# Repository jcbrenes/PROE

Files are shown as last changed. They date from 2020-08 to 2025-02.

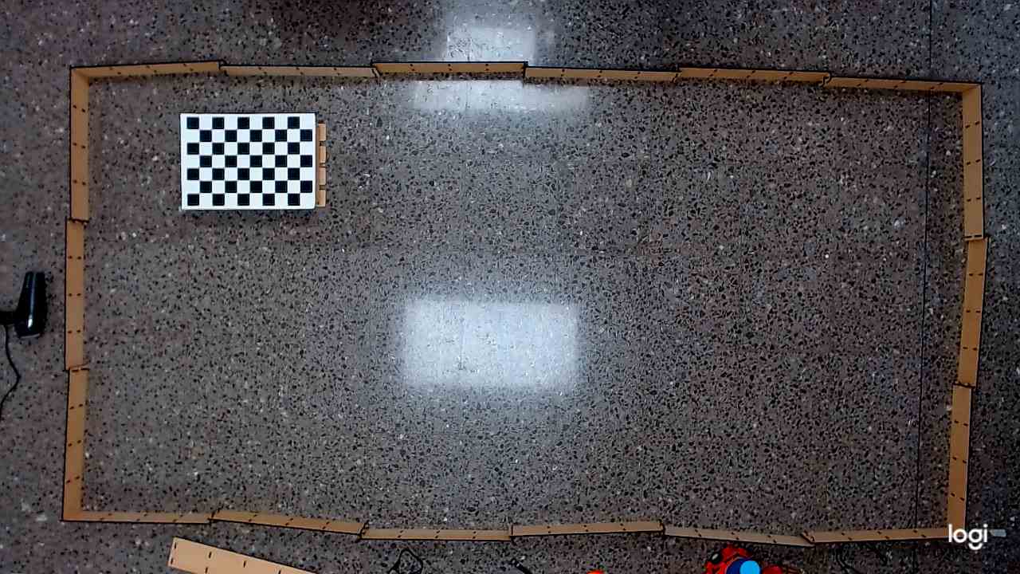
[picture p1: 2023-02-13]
Herramientas/Cámara/VALIDACION_PYTHON/Calibración Python/Imagenes_Calibracion_Nueva_Sala/2022-10-19_15-29-37.jpg

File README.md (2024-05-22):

# Repositorio de software para el proyecto PROE
PROYECTO PROE: Implementación de un prototipo de enjambre de robots para la digitalización de escenarios estáticos y planificación de rutas óptimas.

Proyecto de investigación del Instituto Tecnológico de Costa Rica, dirigido por la Escuela de Matemática y con participación de la Escuela de Ingeniería Mecatrónica.

Este proyecto pretende diseñar un sistema multirobot físico para la exploración de escenarios estáticos desconocidos, con el fin de determinar rutas óptimas. Dicha implementación significa una traducción y adaptación de los algoritmos computacionales de exploración investigados en el proyecto “PROE: Simulación computacional para la planificación de rutas óptimas de acceso y/o evacuación por medio de un enjambre centralizado en escenarios estáticos, utilizando técnicas de mapeo, procesamiento de datos y optimización multiobjetivo” (PROE E1F1 ); además de implementar técnicas de recolección, transferencia y procesamiento de datos para mapear la zona y así poder determinar rutas de acceso y/o evacuación seguras.

Los códigos computacionales, archivos CAD, diagramas eléctricos, esquemas de ensamblaje, lista de materiales y demás documentación acá presente representan el esfuerzo llevado acabo en este proyecto.

Directorio de archivos:
- Arquitectura_PROE-> archivo PDF de la arquitectura del sistema electrónico
- Corte_Chasis_PROE -> archivo PDF para corte láser del chasís 
- Corte_Obstaculos_PROE -> archivo PDF para corte láser de los obstáculos del escenario 
- PCB_Conexiones_PROE-> archivo PDF con la conexiones del PCB
- BOM_PROE -> archivo con la lista de materiales para el proyecto PROE
- EstandarCodigo -> Lineamientos para escritura de código en el proyecto
- Readme 
- LICENSE

Directorio de carpetas:
- PROE_LOCOM -> Proyecto en Arduino IDE (placa Feather M0) para Locomoción y Comunicación
- PROE_DETOB -> Proyecto en Arduino IDE (placa Bluepill STM32) para Detección de Obstáculos
- PROE_COMBASE -> Proyecto en Arduino IDE (placa Feather M0) dispositivo usado como base para la comunicación
- Chasis: archivos CAD para corte láser del chasís
- Obstáculos: archivos CAD para corte láser de los obstáculos
- PCB: archivos CAD para diseño del PCB y archivos Gerber para manufactura del PCB
- Herramientas: archivos para calibración y validación
	- Vision_Validacion -> herramienta de Matlab para validar giros y desplazamientos de un robot
	- Vision_Patron -> archivo PDF del patrón que debe aparecer en las imágenes para calibrar
	- Vision_Guia -> archivo PDF de la figura que debe ubicarse en cada robot para seguimiento
	- Calibracion_Motores -> archivo para correr en feather y calibrar los motores
	- Calibración_Magnetómetro -> archivo para correr en feather y calibrar el magnetómetro

Investigadores: 
- Cindy Calderón Arce (ccalderon@itcr.ac.cr). Escuela de Matemática, Tecnológico de Costa Rica. Coordinadora Proyecto  
- Rebeca Solís Ortega (rsolis@itcr.ac.cr). Escuela de Matemática, Tecnológico de Costa Rica. 
- Juan Carlos Brenes-Torres (juanbrenes@tec.ac.cr). Escuela de Mecatrónica, Tecnológico de Costa Rica. Encargado del desarrollo de software y hardware para los robots AttaBots del proyecto PROE.

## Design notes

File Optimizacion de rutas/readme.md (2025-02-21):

En la carpeta Processing se encuentran los documentos mayormente relacionados al procesamiento de datos.

Dentro se encuentra la carpeta mapeo en donde están todos los archivos. Esto es porque processing tiene la similitud con Arduino de que el archivo mapeo.pde debe estar dentro de una carpeta llamada igual, o sea, mapeo.

En este directorio deben estar las carpetas de videos "1_robot", "2_robot" y "3_robot" que corresponden a procesamiento offline. También está el programa de processing, "mapeo.pde", el cual funciona de la siguiente forma:
1. Se ejecuta el script clickeando en la flecha en la parte superior del programa.
2. Se da click al círculo grande de cada robot para comenzar a seguir ese color.
En ese entonces se crea una carpeta llamada "prueba" (o algo así) dentro de la cual se generan las carpetas "divided_color_matrix" y "reduced_color_matrix", dentro de las cuales, asimismo, se generan las matrices correspondientes, cada 10 segundos. Dentro de esta carpeta se debe poner el video grabado de dicha prueba y nombrar la carpeta de forma adecuada al final de la prueba.

Además, está el programa de R, "Graficas", que se encarga de realizar los gráficos de análisis estadístico con base en los archivos "Principal" y "Resumen". Estos dos archivos son generados por un programa de Python de otra carpeta que se explica a continuación.

----------------------------------------------------------

En la carpeta Python se encuentra el programa para realizar el procesamiento de las matrices generadas por Processing. Si se desea realizar el procesamiento en tiempo real, se debe abrir el programa "main ONLINE.py" después de abrir "mapeo.pde". Este programa genera en la carpeta "prueba" anteriormente mencionada las carpetas "A", "D", "Dict", "Graph", "P" y el archivo "path_objective_Cob", los cuales se van actualizando en tiempo real según la velocidad de procesamiento de la computadora.
OJO esto quiere decir que processing y python son ASINCRÓNICOS.

El programa "análisis_datos.py" accede a las carpetas "1_robot", "2_robot" y "3_robot" mencionadas anteriormente y, asimismo, accede a cada carpeta "5-1", "5-2", ..., "15-13" y toma las matrices de cada prueba para realizar dos informes estadísticos, uno llamado "Principal", el cual contiene las estadísticas descriptivas en cuartiles, y "Resumen", el cual contiene un resumen o promedio de "Principal".

En la carpeta "Procesamiento offline" se encuentran distintos programas según la necesidad, pero en general, el único necesario es "main OFFLINE.py", el cual genera lo mismo que el ONLINE. Los demás se utilizaron una vez, no deberían ser necesarios, pero igual se dejaron por si acaso.

Los demás archivos son dependencias para el main, los cuales no se deben tocar y no es importante explicarlos.

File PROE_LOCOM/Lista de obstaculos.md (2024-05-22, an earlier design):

# Lista de mensajes

Distribución de los mensajes:
- Los mensajes se componen de 7 valores separados por ";" y el orden de lectura es:
	- ID: número de identificación del robot
	- Coordenada X
	- Coordenada Y
	- Orientación
	- Tipo de mensaje
	- Distancia a obstaculo: para sensor sharp
	- Ángulo de obstaculo: para sensor sharp

El tipo de mensaje indica a que se refiere el resto de la información en el mensaje.

Lista de tipos de mensajes que se van a recibir en la base:
- 0: Identifica posición sin obstaculo
- 1: Sharp, da medida de distancia y ángulo
- 2: IR frontal
- 3: IR derecho
- 4: IR izquierdo
- 5: Temperatura
- 6: Batería baja 
- 15: El Atta completó la función avanzarCoordenada y deja de avanzar
- 20: Medición de distancia inicial para coordinación de coordenadas
- 40: Falla de magnetómetro
- 41: Falla de MPU

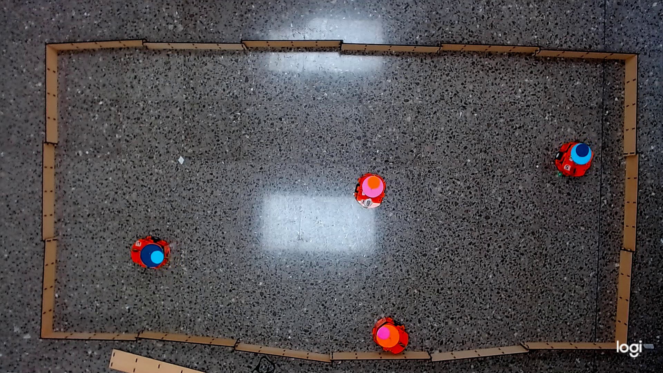
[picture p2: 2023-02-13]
Herramientas/Cámara/VALIDACION_PYTHON/Validación Python/ImagenesRbk/frame34.jpg

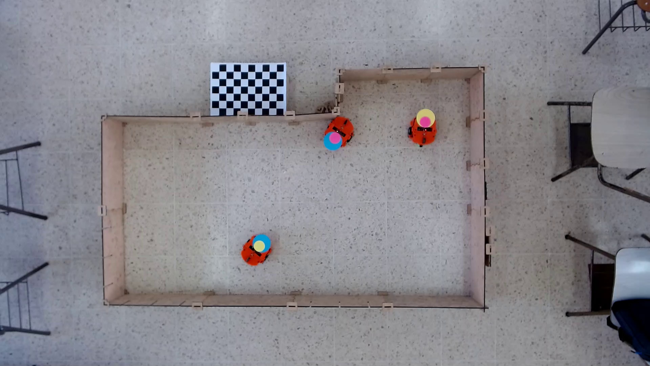
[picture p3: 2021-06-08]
Herramientas/Cámara/VALIDACION_ANTERIOR/Segmentación por color/ImagenesRbk/frame14.jpg

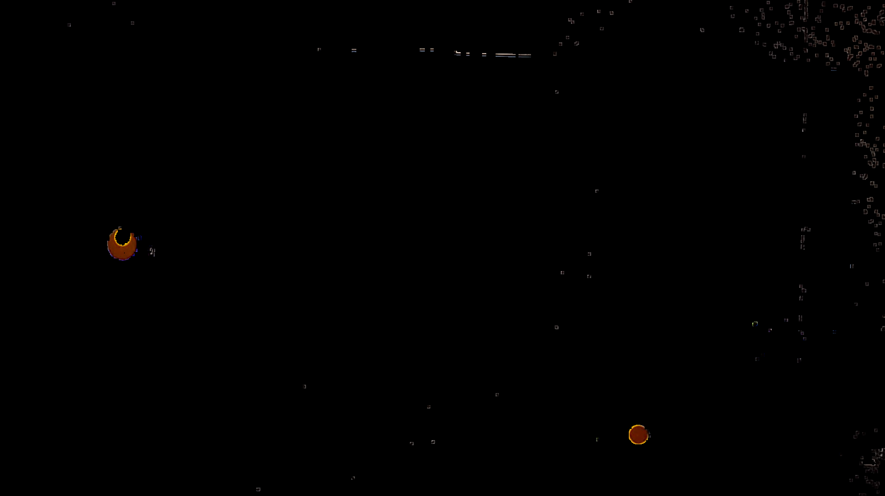
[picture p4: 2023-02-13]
Herramientas/Cámara/VALIDACION_PYTHON/Validación Python/filtrado_azul3.png

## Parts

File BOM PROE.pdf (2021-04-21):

Materiales para la construcción de 1 agente robot de PROE

Cantidad | Nombre | Número parte Link | Costo CR /u
1 | Batería Lipo 2Ah | ADA-328 | https://www.crcibernetica.com/lithium-ion-polymer-battery-3-7v-2500mah/ | $14,95
1 | Boost | ADA-1903 | https://www.crcibernetica.com/powerboost-500-basic-5v-usb-boost-500ma-from-1-8v/ | $10,95
1 | Puente H (módulo) | TB6612FNG | https://www.crcibernetica.com/generic-motor-driver-1a-dual-tb6612fng/ | $4,95
2 | Motores DC encoder | ROB-CB0N20 https://www.crcibernetica.com/n20-gearmotor-with-encoder-and-wheel/ | $14,95
2 | Soporte motores | ROB-CB02443 https://www.crcibernetica.com/micro-gearmotor-support-bracket/ | $0,75
1 | Ball caster | ROB-CB1818 https://www.crcibernetica.com/3pi-n20-ball-caster/ | $2,75
1 | uC Feather M0 RFM69 | ADA-3176 | https://www.crcibernetica.com/adafruit-feather-m0-rfm69-packet-radio-868-or-915-mhz/ | $24,95
1 | Magnetómetro | IM130918001 https://www.crcibernetica.com/hmc5883l-triple-axis-compass-magnetometer-sensor-module/ | $9,95
1 | uC Blue Pill | DEV-CB02143 https://www.crcibernetica.com/stm32f103c8t6-arm-stm32-blue-pill-microcontroller-board/ | $4,95
1 | Servomotor | MG90S | https://www.crcibernetica.com/mg90s-micro-servo-with-metal-gears/ | $6,95
1 | Sensor IR adelante | SEN-CB0006 | https://www.crcibernetica.com/infrared-obstacle-avoidance-module/ | $2,95
2 | Sensor IR abajo | SEN-CB0005 | https://www.crcibernetica.com/track-sensor-module/ | $1,95
1 | Sensor Temperatura | SEN-10988 | https://www.crcibernetica.com/tmp36-temperature-sensor/ | $1,95
1 | Sensor sharp | IM130619002 https://www.crcibernetica.com/sharp-gp2y0a21yk-distance-measuring-sensor/ | $16,95
1 | Pines | PRT-00116 | https://www.crcibernetica.com/break-away-headers-straight/ | $1,95
1 | Interruptor general | COM-CB0372 https://www.crcibernetica.com/slide-switch/ | $1,25
1 | Interruptor pequeño | COM-09609 | https://www.crcibernetica.com/spdt-slide-switch/ | $0,95
1 | LED azul | COM-11372 | https://www.crcibernetica.com/led-basic-blue-5mm/ | $0,15
1 | LED rojo | COM-09594 | https://www.crcibernetica.com/led-basic-yellow-5mm/ | $0,15
1 | LED amarillo | COM-09590 | https://www.crcibernetica.com/led-basic-red-5mm/ | $0,15
1 | IMU | MPU-6050 | https://www.crcibernetica.com/mpu-6050-triple-axis-accelerometer-and-gyroscope-module/ | $6,95
1 | Memoria eeprom | AT24C16 | https://www.microjpm.com/products/at24c16-two-wire-serial-eeprom/ | $1,40
3 | Capacitores poliester 100nF | | https://www.microjpm.com/products/a100if-100v-capacitor-poliester-metalizado/ | $0,40
3 | Header hembra 40 pines 1 fila | | https://www.microjpm.com/products/conector-hembra-de-40pins-2-54mm-una-fila-/ | $0,80
2 | Conector de motor hembra | JST-ZH | https://www.ebay.com/itm/JST-ZH-1-5mm-Pitch-4-Pin-Right-Angle-Male-PCB-Connector-Shrouded-Header-x-100/172462947325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 -
1 | Conector de la bateria | JST-PH | https://www.ebay.com/itm/JST-PH-2-0mm-Pitch-2-Pin-Male-Right-Angle-Connector-Shrouded-Header-Socket-x-100/181461829632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 -
1 | Base DIP 8 pines | https://www.ebay.com/itm/100PCS-DIP8-Integrated-Circuit-8-Pin-IC-Sockets-Adaptor-Solder-Type-New/173695893286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 -
Otros | (Estos componentes se comparten entre varios robots)
Cantidad | Nombre | Modelo | Link | Costo CR
Programador Blue Pill | DEV-CB0468 | https://www.crcibernetica.com/st-link-v2-mini-programmer-color-may-vary/ | $5,95
Cable USB | CAB-10215 | https://www.crcibernetica.com/usb-microb-cable-80-cm/ | $4,95
Caja Espaciadores y tornillos | TOL-CB0513 | https://www.crcibernetica.com/m3-nylon-screw-black-hex-screw-nut-nylon-pcb-standoff-assortment-kit-250pcs/ $15,95
| Caja Resistencias | COM-10969 | https://www.crcibernetica.com/resistor-kit-1-4w-500-total/ | $11,95

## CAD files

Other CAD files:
Chasis/Chasís PROE.dwg
Herramientas/Cámara/VALIDACION_ANTERIOR/Códigos QR/ExportadorCodigosTamañoReal.dwg
Obstaculos/Obstaculos_PROE.dxf
Obstaculos/Obstaculos_PROE.dwg

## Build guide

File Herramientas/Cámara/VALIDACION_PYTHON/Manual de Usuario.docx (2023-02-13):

PROYECTO PROE

Manual de uso del Sistema de Visión (última actualización: 05/02/2023)

CONSIDERACIONES GENERALES

Para ejecutar los códigos se debe tener un ambiente programación como Jupyter Notebooks o Google Colab. Alternativamente, se pueden descargar todas las librerías requeridas y utilizar Python de forma local. Además, se debe contar con el software Logitech Capture para utilizar la webcam.

CALIBRACIÓN

1. Abrir el repositorio de PROE y buscar en la sección Herramientas/Cámara/VALIDACION_PYTHON/Calibracion Python.
2. Se debe disponer de al menos 10 imágenes de calibración utilizando el patrón correspondiente y colocándolo en diferentes posiciones. Las mismas deben ser tomadas con la webcam en la posición definitiva que se vaya a usar. Se adjuntan 4 imágenes a modo de ejemplo:

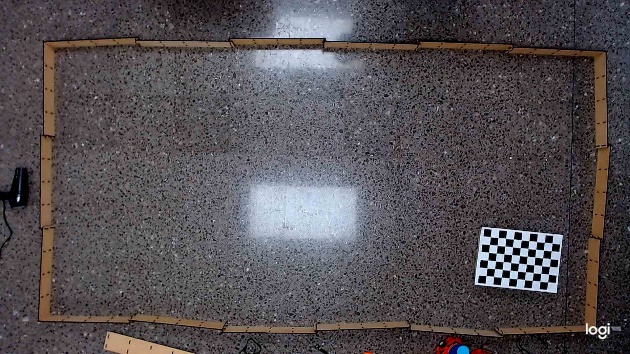
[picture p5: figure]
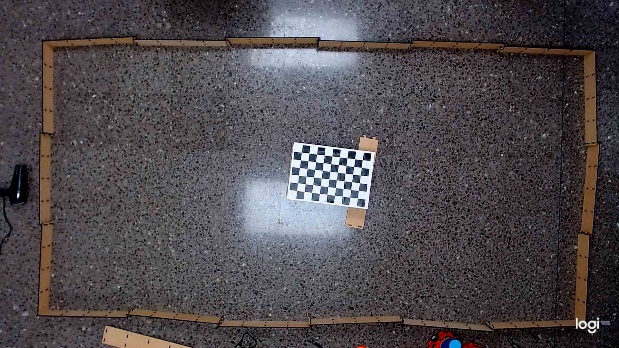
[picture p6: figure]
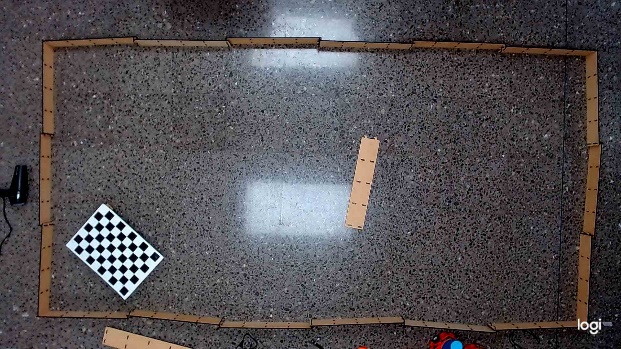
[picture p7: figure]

3. Agregar las imágenes de calibración al folder llamado “Imagenes_Calibracion_Nueva_Sala”.
4. Ejecutar el código llamado “Calibracion_Camara”
5. Se van a generar 2 archivos .txt en el folder, estos corresponden a las matrices de calibración necesarias.
6. Copiar ambos .txt y pegarlos dentro del folder Herramientas/Cámara/VALIDACION_PYTHON/ Validación Python.
7. Al finalizar la calibración, se debe ajustar el ratio de mm/pixeles dentro del código de Validacion. Esto se puede realizar con una de las imágenes de calibración tomadas en el punto 2. Se debe abrir la imagen en Paint, en el mismo se pueden visualizar los pixeles en forma de coordenadas (x,y) en la parte inferior, tal como se muestra en la imagen. Calcular la longitud del lado de un cuadrado del patrón (en pixeles) utilizando la fórmula para la distancia entre 2 puntos. Se sabe de antemano que el lado mide 40 mm.

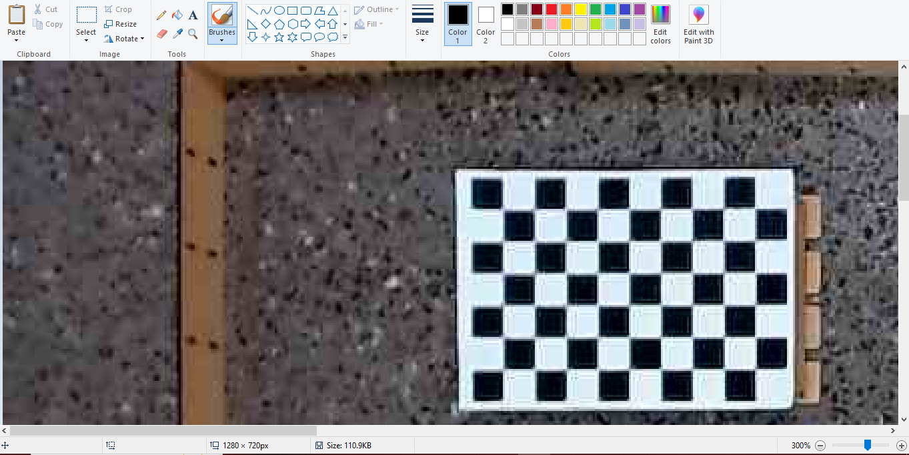
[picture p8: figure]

ratio [mm/pixeles]= (40 mm)/(Longitud del lado en pixeles)

8. Por último, actualizar valor en el código para la variable mmPixel, en ambas líneas. Tal y como se muestra a continuación.

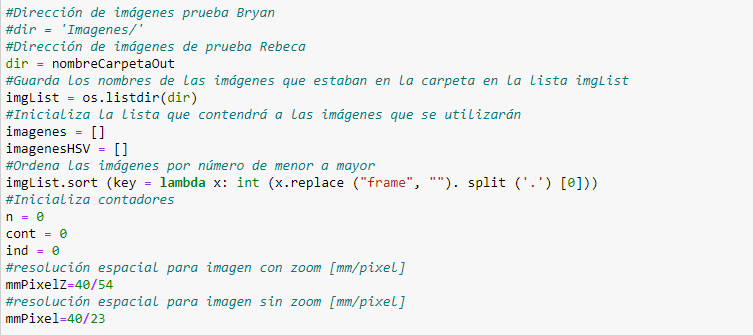
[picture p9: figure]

9. El sistema de visión está listo para ser usado. Se debe agregar un video a la carpeta Herramientas/Cámara/VALIDACION_PYTHON/Validación Python. El nombre se debe actualizar en la variable “nombreVideoIn”. Tener en cuenta las líneas señaladas en azul, dado que cada vez que se ejecuta un nuevo video el código lo descompone en imágenes y las guarda en la carpeta “ImagenesRbk”. Se deben descomentar esta líneas únicamente cuando se cambie de video y adicional a esto, se deben eliminar todas las imágenes de la carpeta “ImagenesRbk” antes de ejecutar el código con un nuevo video.

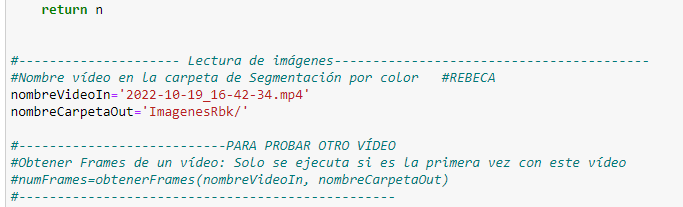
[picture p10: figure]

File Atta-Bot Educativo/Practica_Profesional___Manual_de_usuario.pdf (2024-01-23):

# Instituto Tecnológico de Costa Rica

## Escuela de Computación Ingeniería en Computación Practica profesional

Manual de usuario

## Simplificación de los Atta-Bots para un entorno educativo

## Estudiante:

2018189196 - Isaac David Ortega Arguedas

Fecha de entrega: 7 de Junio, 2023

## I semestre 2023

## Índice

1. Introducción | 2
2. Instalación | 2
3. Ejecución de la aplicación | 4
4. Utilización del programa | 4
5. Desinstalar la aplicación | 14
6. Conclusión | 15

1

## 1. Introducción

El presente documento es el manual de usuario del programa que será entregado por Isaac David Ortega Arguedas, como proyecto de la Practica Profesional para el primer semestre del 2023, a los miembros de investigación PROE, esto es para que tengan material de referencia en caso de tener alguna duda sobre el programa. Este manual va a cubre todos los pasos necesarios para el correcto uso de la aplicación incluyendo el proceso de instalación.

## 2. Instalación

Para instalar la aplicación solo se requiere ejecutar el instalador (ver Figura 1).

Figura 1: Instalador de Atta-Bots-Kids

Una vez ejecutemos el instalador se nos abrirá una ventana (ver Figura 2) en la cual se nos indica que indicara los pasos necesarios para instalar la aplicación. Para proseguir con la instalación pulsamos el botón ”Next”.

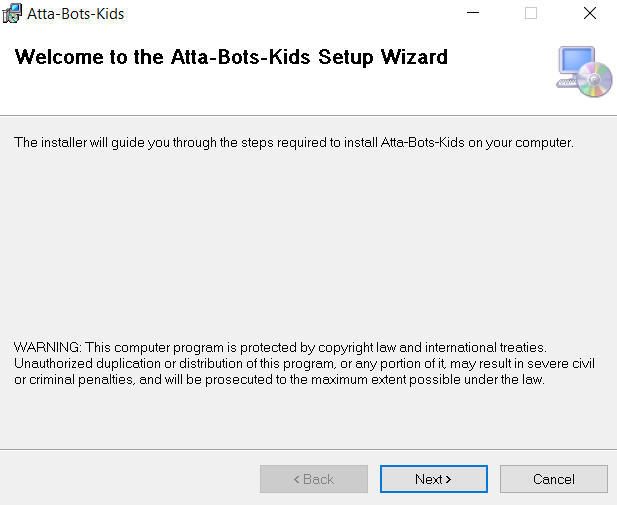
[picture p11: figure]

Figura 2: Confirmar que se quiere instalar la aplicación

En el segundo paso es para indicar donde deseamos instalar la aplicación, así como indicar si deseamos que la aplicación se instale para todos los usuarios de la computadora o solo para el usuario en el que nos encontramos actualmente (ver Figura 3). Ya se cuenta con una dirección por defecto, pero es si se desea cambiar dicha dirección es posible pulsando el botón ”Browse...”. Una vez hayamos escogido la dirección deseada, así como a quienes deseamos instalar la aplicación pulsamos el botón ”Next”.

2

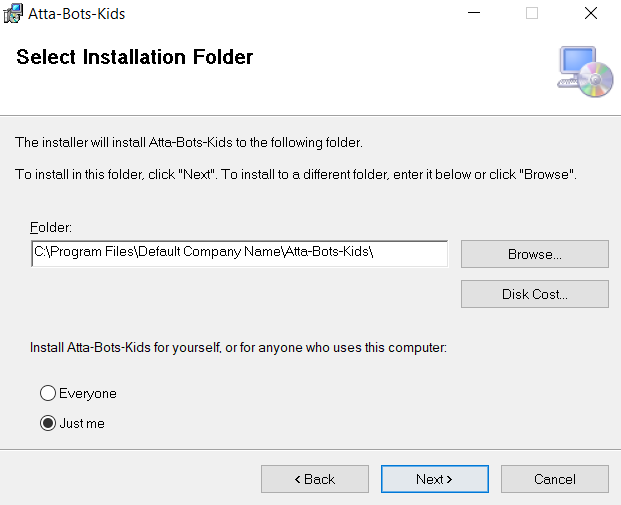
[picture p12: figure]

Figura 3: Se escoge donde se desea instalar la aplicación

Una vez pulsado se nos abrirá una ultima ventana la cual es de confirmación (ver Figura 4). Si estamos seguro de las opciones escogidas en la ventana anterior pulsamos ”Next”, de los contrario podemos pulsar ”Back”para regresar a la ventana anterior. En caso de que deseemos proseguir, se nos abrirá una ventana de Windows preguntando si estamos seguros de querer instalar la aplicación, aceptamos la instalación.

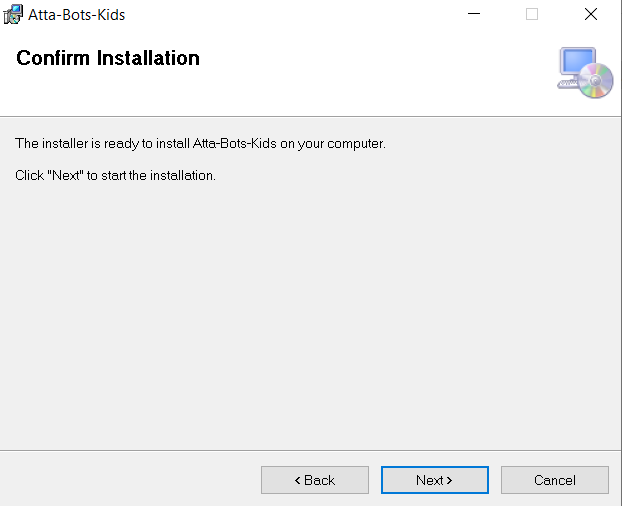
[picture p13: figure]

Figura 4: Confirmar opciones

3

Cuando la instalación haya finalizado se nos abrirá una ultima ventana la cual nos indica que la instalación se realizó correctamente (ver Figura 5). Aquí solo debemos pulsar ”Close”.

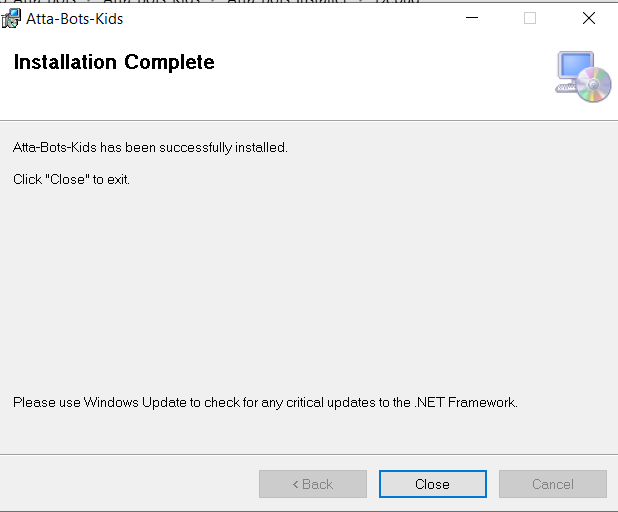
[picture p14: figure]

Figura 5: Mensaje de instalación

Para este punto si nos dirigimos al escritorio podemos observar que apareció una nueva aplicación (ver Figura 6).

Figura 6: Icono de la aplicación

## 3. Ejecución de la aplicación

La ejecución de esta aplicación es igual que cualquier otra.

## 4. Utilización del programa

En esta sección se explicará en detalle todas las funcionalidades con las que cuenta esta aplicación. Se explicará qué acción realiza cada función así como la forma en la que se espera que el usuario interactúe.

### 4.1. Avanzar

El botón que representa esta función (ver Figura 7) es el siguiente.

4

Figura 7: Botón Avanzar

La funcionalidad que cumplen es la de hacer que el Atta-Bot, se mueva hacia adelante. Al momento de interactuar con el botón, una nueva ventana (ver Figura 8) se abrirá. En esta ventana el usuario le indica al sistema cuántos milímetros desea que el Atta-Bot se mueva hacia adelante.

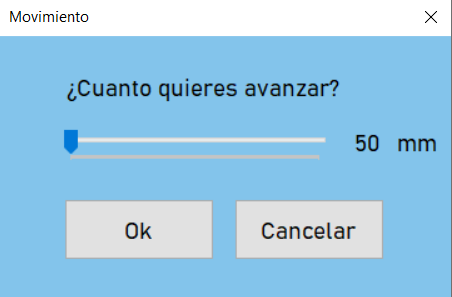
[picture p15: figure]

Figura 8: Cuadro de confirmación avanzar

La forma en la cual el usuario escoge la cantidad de milímetros a avanzar es mediante el slider. Si pulsamos el botón “Ok”, el sistema almacenará la información, se agregará al historial y, cuando se le indique a la aplicación, esta será cargada al Atta-Bot, en caso de que pulse el botón “Cancelar” no pasara nada y se cerrará esta ventana. Lo mínimo que puede avanzar el Atta-Bot son 50 milímetros y el máximo son 999 milímetros.

### 4.2. Retroceder

El botón que representa esta función (ver Figura 9) es el siguiente.

5

Figura 9: Botón Retroceder

La funcionalidad que cumplen es la de hacer que el Atta-Bot, se mueva hacia atrás. Al momento de interactuar con el botón, una nueva ventana (ver Figura
10) se abrirá. En esta ventana el usuario le indica al sistema cuántos milímetros desea que el Atta-Bot se mueva hacia atrás.

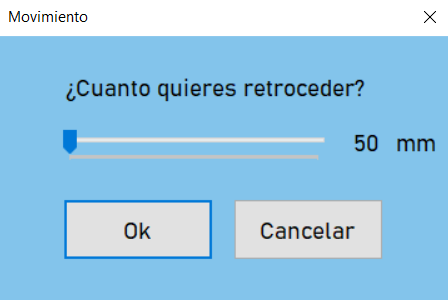
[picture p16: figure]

Figura 10: Cuadro de confirmación retroceder

La forma en la cual el usuario escoge la cantidad de milímetros a retrocer es mediante el slider. Si pulsamos el botón “Ok”, el sistema almacenará la información, se agregará al historial y, cuando se le indique a la aplicación, esta será cargada al Atta-Bot, en caso de que pulse el botón “Cancelar” no pasara nada y se cerrará esta ventana. Lo mínimo que puede retroceder el Atta-Bot son 50 milímetros y el máximo son 999 milímetros.

### 4.3. Girar a la izquierda

El botón que representa esta función (ver Figura 11) es el siguiente.

Figura 11: Botón Girar a la Izquierda

La funcionalidad que cumple es la de hacer que el Atta-Bot gire hacia la izquierda. Al momento de interactuar con alguno el botón aparecerá una nueva ventana (ver Figura 12). En esta ventana el usuario le indica al sistema cuántos grados desea que el Atta-Bot gire a la izquierda.

6

Figura 12: Cuadro de confirmación girar a la izquierda

Si pulsamos el botón “Ok”, el sistema almacenará la información, se agregará al historial y, cuando se le indique a la aplicación, esta será cargada al Atta-Bot, en caso de que pulse el botón “Cancelar” no pasara nada y se cerrará esta ventana. El robot es capaz de hacer giros de 360°, motivo por el cual este es el máximo que puede girar.

### 4.4. Girar a la derecha

El botón que representa esta función (ver Figura 13) es el siguiente.

Figura 13: Botón Girar a la Derecha

La funcionalidad que cumple es la de hacer que el Atta-Bot gire hacia la derecha. Al momento de interactuar con alguno el botón aparecerá una nueva ventana (ver Figura 14). En esta ventana el usuario le indica al sistema cuántos grados desea que el Atta-Bot gire a la derecha.

Figura 14: Cuadro de confirmación girar a la derecha

Si pulsamos el botón “Ok”, el sistema almacenará la información, se agregará al historial y, cuando se le indique a la aplicación, esta será cargada al Atta-Bot, en caso de que pulse el botón “Cancelar” no pasara nada y se cerrará esta ventana. El robot es capaz de hacer giros de 360°, motivo por el cual este es el máximo que puede girar.

7

### 4.5. Activar ciclo

El botón que representa esta función (ver Figura 15) es el siguiente.

Figura 15: Botón Ciclo

La funcionalidad que cumple es que, una vez se haya activado, todas las instrucciones posteriores serán ejecutadas de forma reiterativa. Para facilitar la comprensión de esto, las instrucciones subsecuentes aparecerán más hacia el centro del historial que las instrucciones que no se encuentren dentro del ciclo. Cuando se interactúa con este botón aparecerá una nueva ventana preguntando si deseamos activar un ciclo (ver Figura 16), si se pulsa “Ok” este se activará y el icono cambiará, si se pulsa “Cancelar”, solo se cerrará la ventana.

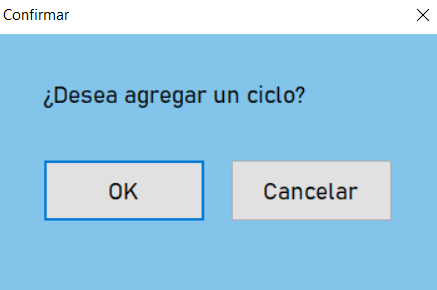
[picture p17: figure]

Figura 16: Cuadro de confirmación agregar ciclo

Una vez el ciclo es activado, la apariencia del botón cambia (ver Figura 17). Esto también es para indicar que el ciclo esta activo.

Figura 17: Botón apagado de Ciclo

Si se pulsa nuevamente sobre el botón aparecerá una nueva ventana la cual preguntará si se desea quitar el ciclo (ver Figura 18). Si pulsamos “Ok” las instrucciones que se hayan agregado después de haberlo activado se moverán a la posición normal y el icono regresará al original. Esto permite mover el ciclo a un punto posterior en la secuencia de instrucciones.

8

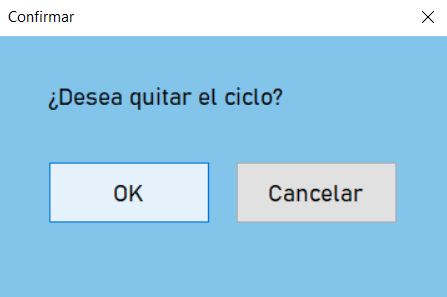
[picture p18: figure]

Figura 18: Cuadro de confirmación quitar ciclo

### 4.6. Detectar obstáculo

El botón que representa esta función (ver Figura 19) es el siguiente.

Figura 19: Botón Obstáculo

La funcionalidad que cumple es que una vez se haya activado el Atta-Bot se detendrá cuando detecte un obstáculo. Cuando se interactúa con este botón aparecerá una nueva ventana preguntando si deseamos detectar obstáculos (ver Figura 20). Si se pulsa “Ok” este se activará y el icono cambiará, si se pulsa “Cancelar”, solo se cerrará la ventana.

Figura 20: Cuadro de confirmación activar detección obstáculos

Una vez la detección de obstáculos es activada, la apariencia del botón cambia (ver Figura 21). Esto con el fin de recordarle al usuario que la detección de obstáculos esta activado.

9

Figura 21: Botón apagado de Obstáculo

Si se pulsa nuevamente sobre el botón aparecerá una nueva ventana la cual preguntará si se desea dejar de detectar obstáculos (ver Figura 22). Si pulsamos “Ok” el Atta-Bot no detendrá la ejecución de las instrucciones cargadas a menos que se le detenga de forma manual, o que haya ejecutado todas las instrucciones cargadas, y el icono regresará al original.

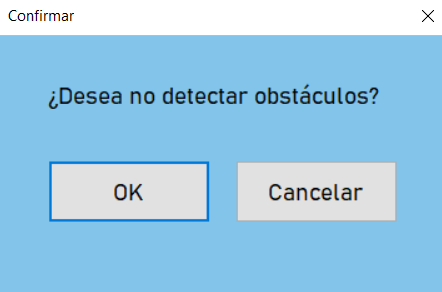
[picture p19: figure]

Figura 22: Cuadro de confirmación desactivar detección obstáculos

### 4.7. Cargar instrucciones

El botón que representa esta función (ver Figura 23) es el siguiente.

Figura 23: Botón Play

La funcionalidad que cumple es la de cargar las instrucciones que se encuentren en el historial al Atta-Bot. Cuando se interactúa con este botón aparecerá una nueva ventana preguntando si deseamos cargar las instrucciones (ver Figura 24), si se pulsa “Ok” las instrucciones se cargan al Atta-Bot y este las empezará a ejecutar, si se pulsa “Cancelar”, solo se cerrará la ventana.

10

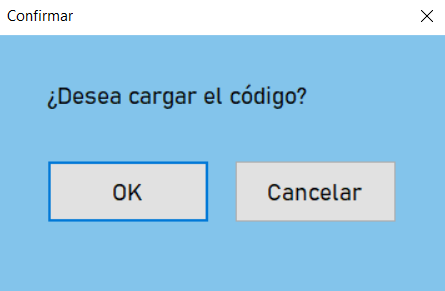
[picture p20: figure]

Figura 24: Cuadro de confirmación cargar código

### 4.8. Detener ejecución

El botón que representa esta función (ver Figura 25) es el siguiente.

Figura 25: Botón Stop

La funcionalidad que cumple es la de detener al Atta-Bot, sin importar qué acción esté realizando. Cuando se interactúa con este botón aparecerá una nueva ventana preguntando si deseamos detener al Atta-Bot (ver Figura 26), si se pulsa “Ok” el Atta-Bot se detendrá, si se pulsa “Cancelar”, solo se cerrará la ventana.

Figura 26: Cuadro de confirmación detener ejecución

### 4.9. Borrar una instrucción en específico

Al momento de agregar nuevas instrucciones estas van a ser representadas de una forma similar a la Figura 27. Si se hace click sobre el botón la instrucción que está relacionada con dicho botón será borrada del historial sin preguntar por ningún tipo de confirmación.

11

Figura 27: Ejemplo de instrucciones en el historial

### 4.10. Limpiar historial

Esta acción puede realizarse mediante dos formas. La primera es pulsando el botón que se asemeja a un basurero (ver Figura 28).

Figura 28: Botón Limpiar

La otra forma es mediante el menú. Primero hacemos click sobre .Archivo ² posteriormente pulsamos ”Limpiar Historial”tal y como se ejemplifica en la Figura 29.

Figura 29: Opción para limpiar el historial

Una vez se haya interactuado de alguna de las dos maneras mencionadas, aparecerá una nueva ventana preguntando si deseamos borrar el historial (ver Figura 30). En caso de pulsar “Ok” las instrucciones del historial se borrarán y, si se llegaron a activar, las opciones de ciclo y detectar obstáculos se desactivaran, si se pulsa “Cancelar”, solo se cerrará la ventana.

12

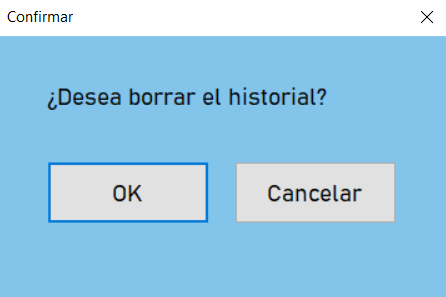
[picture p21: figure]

Figura 30: Cuadro de confirmación borrar historial

### 4.11. Generar documento

Esta función se representa de la siguiente forma (ver Figura 31).

Figura 31: Opción generar documento

La funcionalidad que cumple es la de generar un documento el cual cuente con las instrucciones que se encuentren en el historial en ese momento. Cuando se interactúa con este botón aparecerá una nueva ventana en la cual indicamos donde deseamos guardar el archivo de texto(.txt) y el nombre de dicho archivo (ver Figura 32).

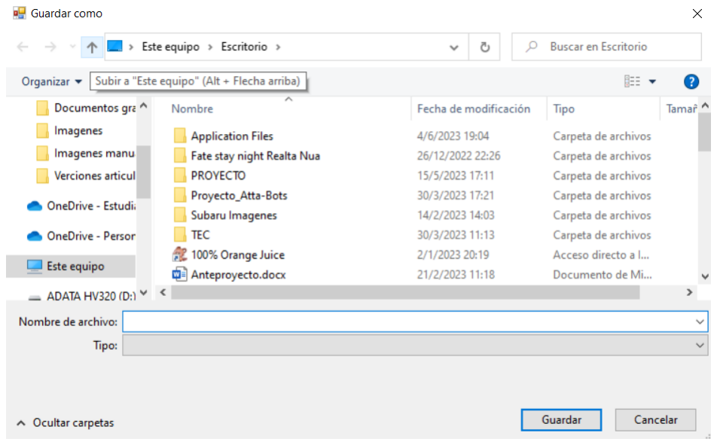
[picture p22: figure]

Figura 32: Seleccionar donde guardar el documento a generar

Si pulsamos “Guardar”se creará un nuevo archivo el cual almacena las instrucciones que se encuentren en el historial. En el caso de que ya exista un archivo de texto con el mismo nombre en el lugar donde se desea guardar, el programa preguntará si se desea sobreescribir el archivo. Por el contrario, si se pulsa “Cancelar” no ocurrirá nada.
La forma en la que las instrucciones se representan en el documento que se acaba de crear es mediante tres letras que representan la instrucción a realizar seguidas por un guión y, después de este guión, se encuentra una secuencia

13 numérica de 1 a 3 dígitos de largo. Las abrebiaciones y se respectiva instrucción son las siguientes: del de delante representa avanzar; atr es para atrás (retroceder); izq de izquierda y der de derecha; obs es para los obstáculos, si el numero que lo acompaña es 0 es que no los detecta, si es 1 sí los detecta; rep de repetir es para indicar el ciclo.

### 4.12. Versión

Esta función se representa de la siguiente forma (ver Figura 33).

Figura 33: Opción versión de la aplicación

Indica la versión actual de la aplicación en una nueva ventana. La ventana es similar a la figura 34.

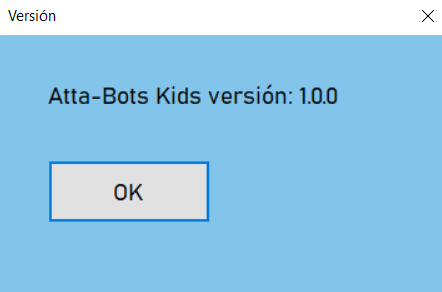
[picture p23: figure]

Figura 34: Versión de la aplicación

### 4.13. Ayuda

Esta función se representa de la siguiente forma (ver Figura 35).

Figura 35: Opción ayuda

Redirige al usuario al manual de usuario, en otras palabras el documento que esta leyendo actualmente.

## 5. Desinstalar la aplicación

Para desinstalar la aplicación, debemos ejecutar el instalador (ver Figura 36). Escogemos la opción para remover la aplicación y pulsamos ”Finish”.

14

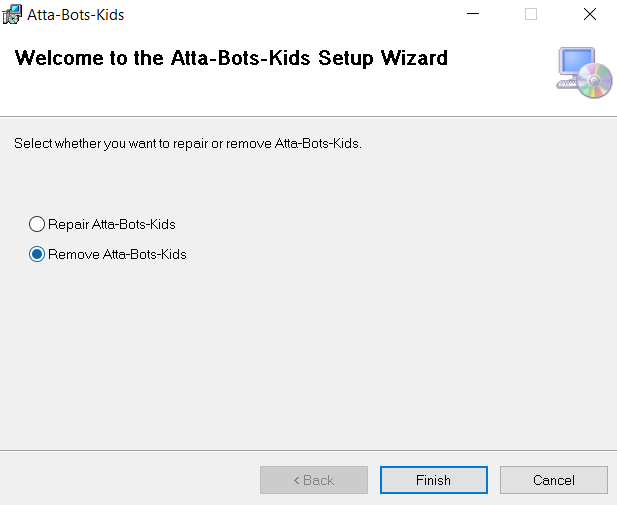
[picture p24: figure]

Figura 36: Mensaje de instalación

## 6. Conclusión

Este programa facilita modificar el comportamiento de los Atta-Bots. Ayudando a su vez a enseñar los principios de la programación de una forma simplificada para que de esta forma eventualmente estos conocimientos se puedan expandir.

15

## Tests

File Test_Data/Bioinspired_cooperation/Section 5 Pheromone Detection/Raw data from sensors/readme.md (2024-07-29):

RAW SENSOR DATA FORMAT

milliseconds Angle_RefSensor(deg) Angle_PheroSensor(deg) Mag_Z_RefSensor(uT) Mag_Z_PheroSensor(uT)

Reference sensor: sensor located up in the robot as reference on magnetic data

Pheromone sensor: sensor located near floor to detect ferrofluid pheromone

Angle: obtained with X and Y axis of magnetic field

Mag_Z: Magnetic field intensity on Z axis

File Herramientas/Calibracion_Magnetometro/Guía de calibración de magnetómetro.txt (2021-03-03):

Proyecto PROE

Guía de calibración de magnetómetro:

1. Abrir el archivo Calibracion_Magnetometro.ino

2. Cargar el código al robot SIN ENCENDERLO (solamente conectar el feather) y desconectarlo luego de que se cargue totalmente

3. Posicionar el robot en un espacio plano donde pueda girar 360° sin ningún problema

4. Verificar que no haya imanes, cables, metales u otros objetos que puedan ocasionar interferencias magnéticas externas

5. Prender el robot y verificar que de una vuelta de 360° lentamente

6. Una vez se detenga, esperar al menos 5 s antes de apagarlo

7. Ya estarían almacenados los valores de calibración en la EEPROM

8. ¡Calibración lista!

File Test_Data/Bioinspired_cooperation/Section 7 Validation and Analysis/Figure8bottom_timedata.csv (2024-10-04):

Exp | Drop_distance | Speed | Coverage_pct | Time
Exp3 | 40mm | 070mm/s | 50,01 | 895
Exp3 | 40mm | 120mm/s | 50,23 | 286
Exp3 | 40mm | 160mm/s | 48,82 | 651,5
Exp4 | 40mm | 160mm/s | 39,26 | 762
Exp4 | 40mm | 160mm/s | 50,55 | 92
Exp3 | 20mm | 070mm/s | 50,06 | 175
Exp3 | 20mm | 120mm/s | 50,06 | 104
Exp3 | 20mm | 160mm/s | 50,13 | 156,5
Exp4 | 20mm | 160mm/s | 50,38 | 250
Exp4 | 20mm | 160mm/s | 50,08 | 125,5
Exp3 | 1mm | 070mm/s | 50,1 | 275
Exp3 | 1mm | 120mm/s | 50,36 | 166,5
Exp3 | 1mm | 160mm/s | 50,77 | 139,5
Exp4 | 1mm | 160mm/s | 50,82 | 138,5
Exp4 | 1mm | 160mm/s | 50,42 | 180

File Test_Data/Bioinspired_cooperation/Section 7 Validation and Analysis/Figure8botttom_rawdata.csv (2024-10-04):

Drop_distance | Speed | Video | Observation | Robot_mov
40mm | 070mm/s | 1 | 1 | Repelled
40mm | 070mm/s | 1 | 2 | Repelled
40mm | 070mm/s | 1 | 3 | Repelled
40mm | 070mm/s | 1 | 4 | Repelled
40mm | 070mm/s | 1 | 5 | Repelled
40mm | 070mm/s | 1 | 6 | Repelled
40mm | 070mm/s | 1 | 7 | Repelled
40mm | 070mm/s | 1 | 8 | Repelled
40mm | 070mm/s | 1 | 9 | Repelled
40mm | 070mm/s | 1 | 10 | Repelled
40mm | 070mm/s | 1 | 11 | Repelled
40mm | 070mm/s | 1 | 12 | Repelled
40mm | 070mm/s | 1 | 13 | Repelled
40mm | 070mm/s | 1 | 14 | Repelled
40mm | 070mm/s | 1 | 15 | Repelled
40mm | 070mm/s | 1 | 16 | Repelled
40mm | 070mm/s | 1 | 17 | Repelled
40mm | 070mm/s | 1 | 18 | Repelled
40mm | 070mm/s | 1 | 19 | Repelled
40mm | 070mm/s | 1 | 20 | Repelled
40mm | 070mm/s | 1 | 1 | Crossed
40mm | 070mm/s | 1 | 2 | Crossed
40mm | 120mm/s | 1 | 1 | Repelled
40mm | 120mm/s | 1 | 2 | Repelled
40mm | 120mm/s | 1 | 3 | Repelled
40mm | 120mm/s | 1 | 4 | Repelled
40mm | 120mm/s | 1 | 5 | Repelled
40mm | 120mm/s | 1 | 6 | Repelled
40mm | 120mm/s | 1 | 7 | Repelled
40mm | 120mm/s | 1 | 8 | Repelled
40mm | 120mm/s | 1 | 9 | Repelled
40mm | 120mm/s | 1 | 10 | Repelled
40mm | 120mm/s | 1 | 11 | Repelled
40mm | 120mm/s | 1 | 12 | Repelled
40mm | 120mm/s | 1 | 13 | Repelled
40mm | 120mm/s | 1 | 14 | Repelled
40mm | 120mm/s | 1 | 15 | Repelled
40mm | 120mm/s | 1 | 16 | Repelled
40mm | 120mm/s | 1 | 17 | Repelled
40mm | 120mm/s | 1 | 18 | Repelled
40mm | 120mm/s | 1 | 19 | Repelled
40mm | 120mm/s | 1 | 20 | Repelled
40mm | 120mm/s | 1 | 21 | Repelled
40mm | 120mm/s | 1 | 22 | Repelled
40mm | 120mm/s | 1 | 1 | Crossed
40mm | 120mm/s | 1 | 2 | Crossed
40mm | 160mm/s | 1 | 1 | Repelled
40mm | 160mm/s | 1 | 2 | Repelled
40mm | 160mm/s | 1 | 3 | Repelled
40mm | 160mm/s | 1 | 4 | Repelled
40mm | 160mm/s | 1 | 5 | Repelled
40mm | 160mm/s | 1 | 6 | Repelled
40mm | 160mm/s | 1 | 7 | Repelled
40mm | 160mm/s | 1 | 8 | Repelled
40mm | 160mm/s | 1 | 9 | Repelled
40mm | 160mm/s | 1 | 10 | Repelled
40mm | 160mm/s | 1 | 11 | Repelled
40mm | 160mm/s | 1 | 12 | Repelled
40mm | 160mm/s | 1 | 13 | Repelled
40mm | 160mm/s | 1 | 14 | Repelled
40mm | 160mm/s | 1 | 15 | Repelled
40mm | 160mm/s | 1 | 16 | Repelled
40mm | 160mm/s | 1 | 17 | Repelled
40mm | 160mm/s | 1 | 18 | Repelled
40mm | 160mm/s | 1 | 19 | Repelled
40mm | 160mm/s | 1 | 1 | Crossed
40mm | 160mm/s | 2 | 1 | Repelled
40mm | 160mm/s | 2 | 2 | Repelled
40mm | 160mm/s | 2 | 3 | Repelled
40mm | 160mm/s | 2 | 4 | Repelled
40mm | 160mm/s | 2 | 5 | Repelled
40mm | 160mm/s | 2 | 6 | Repelled
40mm | 160mm/s | 2 | 7 | Repelled
40mm | 160mm/s | 2 | 8 | Repelled
40mm | 160mm/s | 2 | 9 | Repelled
40mm | 160mm/s | 2 | 10 | Repelled
40mm | 160mm/s | 2 | 11 | Repelled
40mm | 160mm/s | 2 | 12 | Repelled
40mm | 160mm/s | 2 | 13 | Repelled
40mm | 160mm/s | 2 | 14 | Repelled
40mm | 160mm/s | 2 | 15 | Repelled
40mm | 160mm/s | 2 | 16 | Repelled
40mm | 160mm/s | 2 | 17 | Repelled
40mm | 160mm/s | 2 | 18 | Repelled
40mm | 160mm/s | 2 | 19 | Repelled
40mm | 160mm/s | 2 | 1 | Crossed
40mm | 160mm/s | 3 | 1 | Repelled
40mm | 160mm/s | 3 | 2 | Repelled
40mm | 160mm/s | 3 | 3 | Repelled
40mm | 160mm/s | 3 | 4 | Repelled
40mm | 160mm/s | 3 | 5 | Repelled
40mm | 160mm/s | 3 | 6 | Repelled
40mm | 160mm/s | 3 | 7 | Repelled
40mm | 160mm/s | 3 | 8 | Repelled
40mm | 160mm/s | 3 | 9 | Repelled
40mm | 160mm/s | 3 | 10 | Repelled
40mm | 160mm/s | 3 | 11 | Repelled
40mm | 160mm/s | 3 | 12 | Repelled
40mm | 160mm/s | 3 | 13 | Repelled
40mm | 160mm/s | 3 | 14 | Repelled
40mm | 160mm/s | 3 | 15 | Repelled
40mm | 160mm/s | 3 | 16 | Repelled
40mm | 160mm/s | 3 | 17 | Repelled
40mm | 160mm/s | 3 | 18 | Repelled
40mm | 160mm/s | 3 | 19 | Repelled
40mm | 160mm/s | 3 | 20 | Repelled
40mm | 160mm/s | 3 | 1 | Crossed
20mm | 070mm/s | 1 | 1 | Repelled
20mm | 070mm/s | 1 | 2 | Repelled
20mm | 070mm/s | 1 | 3 | Repelled
20mm | 070mm/s | 1 | 4 | Repelled
20mm | 070mm/s | 1 | 5 | Repelled
20mm | 070mm/s | 1 | 6 | Repelled
20mm | 070mm/s | 1 | 7 | Repelled
20mm | 070mm/s | 1 | 8 | Repelled
20mm | 070mm/s | 1 | 9 | Repelled
20mm | 070mm/s | 1 | 10 | Repelled
20mm | 070mm/s | 1 | 11 | Repelled
20mm | 070mm/s | 1 | 12 | Repelled
20mm | 070mm/s | 1 | 13 | Repelled
20mm | 070mm/s | 1 | 14 | Repelled
20mm | 070mm/s | 1 | 15 | Repelled
20mm | 070mm/s | 1 | 16 | Repelled
20mm | 070mm/s | 1 | 17 | Repelled
20mm | 070mm/s | 1 | 18 | Repelled
20mm | 070mm/s | 1 | 19 | Repelled
20mm | 070mm/s | 1 | 20 | Repelled
20mm | 070mm/s | 1 | 21 | Repelled
20mm | 070mm/s | 1 | 22 | Repelled
20mm | 120mm/s | 1 | 1 | Repelled
20mm | 120mm/s | 1 | 2 | Repelled
20mm | 120mm/s | 1 | 3 | Repelled
20mm | 120mm/s | 1 | 4 | Repelled
20mm | 120mm/s | 1 | 5 | Repelled
20mm | 120mm/s | 1 | 6 | Repelled
20mm | 120mm/s | 1 | 7 | Repelled
20mm | 120mm/s | 1 | 8 | Repelled
20mm | 120mm/s | 1 | 9 | Repelled
20mm | 120mm/s | 1 | 10 | Repelled
20mm | 120mm/s | 1 | 11 | Repelled
20mm | 120mm/s | 1 | 12 | Repelled
20mm | 120mm/s | 1 | 13 | Repelled
20mm | 120mm/s | 1 | 14 | Repelled
20mm | 120mm/s | 1 | 15 | Repelled
20mm | 120mm/s | 1 | 16 | Repelled
20mm | 120mm/s | 1 | 17 | Repelled
20mm | 120mm/s | 1 | 18 | Repelled
20mm | 120mm/s | 1 | 19 | Repelled
20mm | 120mm/s | 1 | 20 | Repelled
20mm | 120mm/s | 1 | 21 | Repelled
20mm | 160mm/s | 1 | 1 | Repelled
20mm | 160mm/s | 1 | 2 | Repelled
20mm | 160mm/s | 1 | 3 | Repelled
20mm | 160mm/s | 1 | 4 | Repelled
20mm | 160mm/s | 1 | 5 | Repelled
20mm | 160mm/s | 1 | 6 | Repelled
20mm | 160mm/s | 1 | 7 | Repelled
20mm | 160mm/s | 1 | 8 | Repelled
20mm | 160mm/s | 1 | 9 | Repelled
20mm | 160mm/s | 1 | 10 | Repelled
20mm | 160mm/s | 1 | 11 | Repelled
20mm | 160mm/s | 1 | 12 | Repelled
20mm | 160mm/s | 1 | 13 | Repelled
20mm | 160mm/s | 1 | 14 | Repelled
20mm | 160mm/s | 1 | 15 | Repelled
20mm | 160mm/s | 1 | 16 | Repelled
20mm | 160mm/s | 1 | 17 | Repelled
20mm | 160mm/s | 1 | 18 | Repelled
20mm | 160mm/s | 1 | 19 | Repelled
20mm | 160mm/s | 1 | 20 | Repelled
20mm | 160mm/s | 1 | 1 | Crossed
20mm | 160mm/s | 2 | 1 | Repelled
20mm | 160mm/s | 2 | 2 | Repelled
20mm | 160mm/s | 2 | 3 | Repelled
20mm | 160mm/s | 2 | 4 | Repelled
20mm | 160mm/s | 2 | 5 | Repelled
20mm | 160mm/s | 2 | 6 | Repelled
20mm | 160mm/s | 2 | 7 | Repelled
20mm | 160mm/s | 2 | 8 | Repelled
20mm | 160mm/s | 2 | 9 | Repelled
20mm | 160mm/s | 2 | 10 | Repelled
20mm | 160mm/s | 2 | 11 | Repelled
20mm | 160mm/s | 2 | 12 | Repelled
20mm | 160mm/s | 2 | 13 | Repelled
20mm | 160mm/s | 2 | 14 | Repelled
20mm | 160mm/s | 2 | 15 | Repelled
20mm | 160mm/s | 2 | 16 | Repelled
20mm | 160mm/s | 2 | 17 | Repelled
20mm | 160mm/s | 2 | 18 | Repelled
20mm | 160mm/s | 2 | 19 | Repelled
20mm | 160mm/s | 2 | 20 | Repelled
20mm | 160mm/s | 2 | 21 | Repelled
20mm | 160mm/s | 3 | 1 | Repelled
20mm | 160mm/s | 3 | 2 | Repelled
20mm | 160mm/s | 3 | 3 | Repelled
20mm | 160mm/s | 3 | 4 | Repelled
20mm | 160mm/s | 3 | 5 | Repelled
20mm | 160mm/s | 3 | 6 | Repelled
20mm | 160mm/s | 3 | 7 | Repelled
20mm | 160mm/s | 3 | 8 | Repelled
20mm | 160mm/s | 3 | 9 | Repelled
20mm | 160mm/s | 3 | 10 | Repelled
20mm | 160mm/s | 3 | 11 | Repelled
20mm | 160mm/s | 3 | 12 | Repelled
20mm | 160mm/s | 3 | 13 | Repelled
20mm | 160mm/s | 3 | 14 | Repelled
20mm | 160mm/s | 3 | 15 | Repelled
20mm | 160mm/s | 3 | 16 | Repelled
20mm | 160mm/s | 3 | 17 | Repelled
20mm | 160mm/s | 3 | 18 | Repelled
20mm | 160mm/s | 3 | 19 | Repelled
20mm | 160mm/s | 3 | 20 | Repelled
20mm | 160mm/s | 3 | 21 | Repelled
1mm | 070mm/s | 1 | 1 | Repelled
1mm | 070mm/s | 1 | 2 | Repelled
1mm | 070mm/s | 1 | 3 | Repelled
1mm | 070mm/s | 1 | 4 | Repelled
1mm | 070mm/s | 1 | 5 | Repelled
1mm | 070mm/s | 1 | 6 | Repelled
1mm | 070mm/s | 1 | 7 | Repelled
1mm | 070mm/s | 1 | 8 | Repelled
1mm | 070mm/s | 1 | 9 | Repelled
1mm | 070mm/s | 1 | 10 | Repelled
1mm | 070mm/s | 1 | 11 | Repelled
1mm | 070mm/s | 1 | 12 | Repelled
1mm | 070mm/s | 1 | 13 | Repelled
1mm | 070mm/s | 1 | 14 | Repelled
1mm | 070mm/s | 1 | 15 | Repelled
1mm | 070mm/s | 1 | 16 | Repelled
1mm | 070mm/s | 1 | 17 | Repelled
1mm | 070mm/s | 1 | 18 | Repelled
1mm | 070mm/s | 1 | 19 | Repelled
1mm | 070mm/s | 1 | 20 | Repelled
1mm | 070mm/s | 1 | 21 | Repelled
1mm | 070mm/s | 1 | 22 | Repelled
1mm | 120mm/s | 1 | 1 | Repelled
1mm | 120mm/s | 1 | 2 | Repelled
1mm | 120mm/s | 1 | 3 | Repelled
1mm | 120mm/s | 1 | 4 | Repelled
1mm | 120mm/s | 1 | 5 | Repelled
1mm | 120mm/s | 1 | 6 | Repelled
1mm | 120mm/s | 1 | 7 | Repelled
1mm | 120mm/s | 1 | 8 | Repelled
1mm | 120mm/s | 1 | 9 | Repelled
1mm | 120mm/s | 1 | 10 | Repelled
1mm | 120mm/s | 1 | 11 | Repelled
1mm | 120mm/s | 1 | 12 | Repelled
1mm | 120mm/s | 1 | 13 | Repelled
1mm | 120mm/s | 1 | 14 | Repelled
1mm | 120mm/s | 1 | 15 | Repelled
1mm | 120mm/s | 1 | 16 | Repelled
1mm | 120mm/s | 1 | 17 | Repelled
1mm | 120mm/s | 1 | 18 | Repelled
1mm | 120mm/s | 1 | 19 | Repelled
1mm | 120mm/s | 1 | 20 | Repelled
1mm | 120mm/s | 1 | 21 | Repelled
1mm | 120mm/s | 1 | 22 | Repelled
1mm | 160mm/s | 1 | 1 | Repelled
1mm | 160mm/s | 1 | 2 | Repelled
1mm | 160mm/s | 1 | 3 | Repelled
1mm | 160mm/s | 1 | 4 | Repelled
1mm | 160mm/s | 1 | 5 | Repelled
1mm | 160mm/s | 1 | 6 | Repelled
1mm | 160mm/s | 1 | 7 | Repelled
1mm | 160mm/s | 1 | 8 | Repelled
1mm | 160mm/s | 1 | 9 | Repelled
1mm | 160mm/s | 1 | 10 | Repelled
1mm | 160mm/s | 1 | 11 | Repelled
1mm | 160mm/s | 1 | 12 | Repelled
1mm | 160mm/s | 1 | 13 | Repelled
1mm | 160mm/s | 1 | 14 | Repelled
1mm | 160mm/s | 1 | 15 | Repelled
1mm | 160mm/s | 1 | 16 | Repelled
1mm | 160mm/s | 1 | 17 | Repelled
1mm | 160mm/s | 1 | 18 | Repelled
1mm | 160mm/s | 1 | 19 | Repelled
1mm | 160mm/s | 1 | 20 | Repelled
1mm | 160mm/s | 1 | 21 | Repelled
1mm | 160mm/s | 1 | 22 | Repelled
1mm | 160mm/s | 2 | 1 | Repelled
1mm | 160mm/s | 2 | 2 | Repelled
1mm | 160mm/s | 2 | 3 | Repelled
1mm | 160mm/s | 2 | 4 | Repelled
1mm | 160mm/s | 2 | 5 | Repelled
1mm | 160mm/s | 2 | 6 | Repelled
1mm | 160mm/s | 2 | 7 | Repelled
1mm | 160mm/s | 2 | 8 | Repelled
1mm | 160mm/s | 2 | 9 | Repelled
1mm | 160mm/s | 2 | 10 | Repelled
1mm | 160mm/s | 2 | 11 | Repelled
1mm | 160mm/s | 2 | 12 | Repelled
1mm | 160mm/s | 2 | 13 | Repelled
1mm | 160mm/s | 2 | 14 | Repelled
1mm | 160mm/s | 2 | 15 | Repelled
1mm | 160mm/s | 2 | 16 | Repelled
1mm | 160mm/s | 2 | 17 | Repelled
1mm | 160mm/s | 2 | 18 | Repelled
1mm | 160mm/s | 2 | 19 | Repelled
1mm | 160mm/s | 2 | 20 | Repelled
1mm | 160mm/s | 2 | 21 | Repelled
1mm | 160mm/s | 3 | 1 | Repelled
1mm | 160mm/s | 3 | 2 | Repelled
1mm | 160mm/s | 3 | 3 | Repelled
1mm | 160mm/s | 3 | 4 | Repelled
1mm | 160mm/s | 3 | 5 | Repelled
1mm | 160mm/s | 3 | 6 | Repelled
1mm | 160mm/s | 3 | 7 | Repelled
1mm | 160mm/s | 3 | 8 | Repelled
1mm | 160mm/s | 3 | 9 | Repelled
1mm | 160mm/s | 3 | 10 | Repelled
1mm | 160mm/s | 3 | 11 | Repelled
1mm | 160mm/s | 3 | 12 | Repelled
1mm | 160mm/s | 3 | 13 | Repelled
1mm | 160mm/s | 3 | 14 | Repelled
1mm | 160mm/s | 3 | 15 | Repelled
1mm | 160mm/s | 3 | 16 | Repelled
1mm | 160mm/s | 3 | 17 | Repelled
1mm | 160mm/s | 3 | 18 | Repelled
1mm | 160mm/s | 3 | 19 | Repelled
1mm | 160mm/s | 3 | 20 | Repelled
1mm | 160mm/s | 3 | 21 | Repelled

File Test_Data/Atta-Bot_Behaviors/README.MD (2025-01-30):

**Atta-Bots: Adaptaciones, comportamientos y funcionalidades en el marco de los proyectos PROE**

Proyecto de investigación Atta-Bots del Tecnológico de Costa Rica (código VIE 5402-1440-5101), con participación de la Escuela de Matemática y la Escuela de Ingeniería Mecatrónica.

Objetivo:
Diseñar nuevos comportamientos y funcionalidades en los Atta-Bots construidos en PROE: E1F2 para disminuir la incertidumbre entre lo simulado y lo real.

Período de ejecución:
Enero 2022 - Diciembre 2023

Equipo investigador:

Cindy Calderón Arce. ORCID: https://orcid.org/0000-0002-0077-225X

Rebeca Solís Ortega. ORCID: https://orcid.org/0000-0002-3065-8386

Juan Carlos Brenes Torres. ORCID: https://orcid.org/0000-0001-6323-2173

Repositorio de: 

Código computacional de comunicación entre robots.

Código computacional de mapeo en tiempo real.

Código computacional de generación de rutas óptimas en tiempo real.

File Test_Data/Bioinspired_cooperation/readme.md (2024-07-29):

Data for article: 
Bioinspired cooperation in an heterogeneous robot swarm using ferrofluid artificial pheromones for uncontrolled environments

Authors:
Juan Carlos Brenes-Torres
Cindy Calderón-Arce
Francisco Blanes
José Simó

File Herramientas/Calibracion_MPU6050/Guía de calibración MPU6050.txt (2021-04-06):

Proyecto PROE

Guía de calibración de MPU6050:

1. Abrir el código de calibración MPU

2. Colocar el robot en una superficie lo más horizontal posible, si es posible usen un nivel para verificar

3. Abrir el monitor serial y correr el código

4. Debería aparecer un mensaje en el monitor: "Datos guardados con exito"

5. ¡Calibración lista! Los valores ya deberían estar almacenados en la EEPROM

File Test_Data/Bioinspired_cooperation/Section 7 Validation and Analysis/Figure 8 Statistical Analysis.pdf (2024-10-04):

Figure 8 Statistical Analysis

ROBOT INTERACTIONS

Logistic Binary Regression
Input: Drop distance and Speed
Output: Robot Interactions (for “Repelled”) Deviance Residuals:
Min | 1Q | Median | 3Q | Max
-0.40643 | -0.34289 | -0.12842 | -0.00005 | 3.09909

Coefficients:
Estimate Std. Error z value Pr(>|z|)
(Intercept) | -20.35132 1703.49171 | -0.012 | 0.990
Drop_distance20mm | 15.90942 1703.49189 | 0.009 | 0.993
Drop_distance40mm | 17.89905 1703.49164 | 0.011 | 0.992
Speed120mm/s | -0.07615 | 1.03636 | -0.073 | 0.941
Speed160mm/s | -0.35202 | 0.89519 | -0.393 | 0.694

(Dispersion parameter for binomial family taken to be 1)

Null deviance: 74.871 | on 320 | degrees of freedom
Residual deviance: 62.837 | on 316 | degrees of freedom
AIC: 72.837

Number of Fisher Scoring iterations: 19

Chi-Square Test
Input: Drop distance
Output: Robot Interactions
Pearson's Chi-squared test X-squared = 11.028, df = 2, p-value = 0.004029

Chi-Square Test
Input: Speed
Output: Robot Interactions
Pearson's Chi-squared test X-squared = 0.24843, df = 2, p-value = 0.8832

Table of Output count by Drop distance Repelled Crossed
1mm | 108 | 0
20mm | 105 | 1
40mm | 100 | 7

Table of Output proportion by Drop distance
Repelled | Crossed
1mm | 1.000000000 0.000000000
20mm 0.990566038 0.009433962
40mm 0.934579439 0.065420561

TIME FOR 50% COVERAGE

One-way ANOVA
Input: Drop distance
Output: Time for 50% coverage (Time)
Df Sum Sq Mean Sq F value Pr(>F)
Drop_distance | 2 447913 | 223957 | 5.621 0.0189 *
Residuals | 12 478134 | 39844
Signif. codes: 0 ‘***’ 0.001 ‘**’ 0.01 ‘*’ 0.05 ‘.’ 0.1 ‘ ’ 1

Assumption for ANOVA test: Normality
Output: Time for 50% coverage (Time)

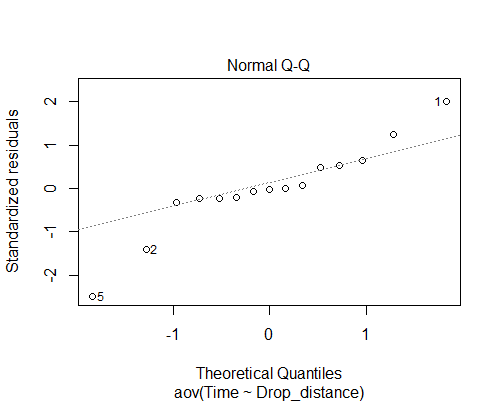
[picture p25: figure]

Assumption for ANOVA test: Homogeneity of variances Levene's Test
Input: Drop distance
Output: Time for 50% coverage (Time)
Levene's Test for Homogeneity of Variance (center = median) Df F value Pr(>F)
group | 2 | 4.6993 0.0311 *
| 12
Signif. codes: 0 ‘***’ 0.001 ‘**’ 0.01 ‘*’ 0.05 ‘.’ 0.1 ‘ ’ 1

Welch's ANOVA test
One-way analysis of means (not assuming equal variances)

data: Time and Drop_distance
F = 2.786, num df = 2.0000, denom df = 7.1754, p-value = 0.1272

QUANTITY OF INTERACTIONS BY ROBOT

One-way ANOVA
Input: Robot
Output: Quantity of interactions
Df Sum Sq Mean Sq F value Pr(>F)
Robot | 2 | 32.07 | 16.033 | 1.712 | 0.2
Residuals | 27 252.90 | 9.367

Assumption for ANOVA test: Normality Output: Quantity of interactions

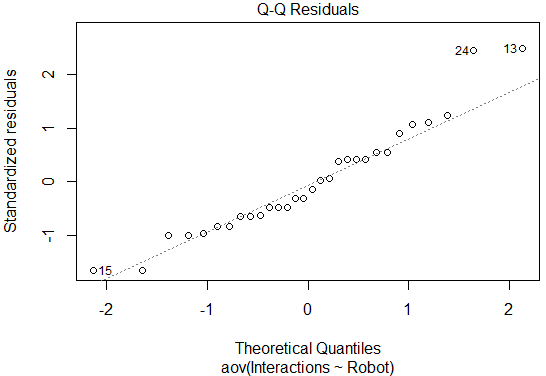
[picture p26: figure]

Assumption for ANOVA test: Homogeneity of variances Levene's Test
Input: Robot
Output: Quantity of interactions
Levene's Test for Homogeneity of Variance (center = median) Df F value Pr(>F)
group | 2 | 0.597 0.5576
| 27

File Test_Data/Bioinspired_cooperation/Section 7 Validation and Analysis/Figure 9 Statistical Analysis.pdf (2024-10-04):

Figure 9 Statistical Analysis

Two-way ANOVA
Input: Concentration and Speed
Output: Magnetic Field Intensity
Df | Sum Sq Mean Sq F value Pr(>F)
Concentration | 2 | 69495 | 34747 | 1.967 | 0.146
Speed | 2 | 64275 | 32138 | 1.820 | 0.169
Concentration:Speed | 4 | 139471 | 34868 | 1.974 | 0.106
Residuals | 81 1430674 | 17663

Two-way ANOVA
Input: Concentration and Speed
Output: Time Period
Df Sum Sq Mean Sq F value | Pr(>F)
Concentration | 2 0.3643 0.18217 | 4.697 0.01175 *
Speed | 2 0.3795 0.18974 | 4.892 0.00987 **
Concentration:Speed | 4 0.6746 0.16865 | 4.349 0.00309 **
Residuals | 81 3.1414 0.03878
Signif. codes: 0 ‘***’ 0.001 ‘**’ 0.01 ‘*’ 0.05 ‘.’ 0.1 ‘ ’ 1

Assumption for ANOVA test: Normality
Output: Magnetic Field Intensity (H_max) and Time Period (T_H)

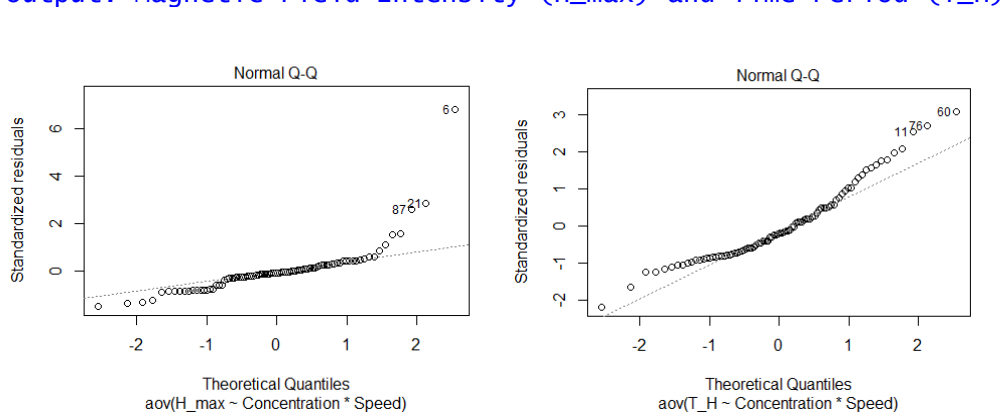
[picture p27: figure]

Assumption for ANOVA test: Homogeneity of variances

Levene's Test
Input: Concentration and Speed
Output: Magnetic Field Intensity
Levene's Test for Homogeneity of Variance (center = median)
Df F value | Pr(>F)
group | 8 | 1.8524 0.07916 .
| 81
Signif. codes: 0 ‘***’ 0.001 ‘**’ 0.01 ‘*’ 0.05 ‘.’ 0.1 ‘ ’ 1

Levene's Test
Two-way ANOVA
Input: Concentration and Speed
Output: Time Period
Levene's Test for Homogeneity of Variance (center = median) Df F value Pr(>F)
group | 8 | 1.5737 0.1457
| 81

Kruskal-Wallis rank sum test for Magnetic Field Intensity (H_max) data: H_max by Concentration
Kruskal-Wallis chi-squared = 2.7893, df = 2, p-value = 0.2479 data: H_max by Speed
Kruskal-Wallis chi-squared = 2.5221, df = 2, p-value = 0.2834

Linear model of Time Period (T_H)

Residuals:
Min | 1Q | Median | 3Q | Max
-0.41030 -0.13965 -0.03850 | 0.09158 | 0.57460

Coefficients:
Estimate Std. Error t value Pr(>|t|)
(Intercept) | 0.61030 | 0.06228 | 9.800 2.10e-15 ***
Concentration07ml | -0.41910 | 0.08807 | -4.759 8.39e-06 ***
Concentration10ml | -0.33250 | 0.08807 | -3.775 0.000303 ***
Speed120mm/s | -0.33530 | 0.08807 | -3.807 0.000272 ***
Speed160mm/s | -0.41370 | 0.08807 | -4.697 1.06e-05 ***
Concentration07ml:Speed120mm/s | 0.37830 | 0.12455 | 3.037 0.003211 **
Concentration10ml:Speed120mm/s | 0.28490 | 0.12455 | 2.287 0.024781 *
Concentration07ml:Speed160mm/s | 0.48190 | 0.12455 | 3.869 0.000220 ***
Concentration10ml:Speed160mm/s | 0.30030 | 0.12455 | 2.411 0.018170 *
Signif. codes: 0 ‘***’ 0.001 ‘**’ 0.01 ‘*’ 0.05 ‘.’ 0.1 ‘ ’ 1

Residual standard error: 0.1969 on 81 degrees of freedom
Multiple R-squared: | 0.3111, | Adjusted R-squared: | 0.243
F-statistic: 4.572 on 8 and 81 DF, | p-value: 0.0001266

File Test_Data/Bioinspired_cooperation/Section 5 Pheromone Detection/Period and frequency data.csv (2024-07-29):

 |  | Period (ms) |  |  |  |  |  | Frecuency (Hz)
Location | Drop | Measurement 1 | Measurement 2 | Measurement 3 | Measurement 4 | Measurement 5 | Measurement 6 | Measurement 1 | Measurement 2 | Measurement 3 | Measurement 4 | Measurement 5 | Measurement 6
CUARTO | 1 | 118 | 129 | 127 | 126 | 118 | 130 | 8,4746 | 7,7519 | 7,874 | 7,9365 | 8,4746 | 7,6923
CUARTO | 2 | 126 | 120 | 119 | 130 | 129 | 119 | 7,9365 | 8,3333 | 8,4034 | 7,6923 | 7,7519 | 8,4034
CUARTO | 3 | 120 | 130 | 125 | 127 | 128 | 117 | 8,3333 | 7,6923 | 8 | 7,874 | 7,8125 | 8,547
CUARTO | 4 | 116 | 121 | 119 | 127 | 119 | 128 | 8,6207 | 8,2645 | 8,4034 | 7,874 | 8,4034 | 7,8125
CUARTO | 5 | 124 | 127 | 125 | 125 | 120 | 129 | 8,0645 | 7,874 | 8 | 8 | 8,3333 | 7,7519
CUARTO | 6 | 127 | 123 | 123 | 124 | 122 | 130 | 7,874 | 8,1301 | 8,1301 | 8,0645 | 8,1967 | 7,6923
CUARTO | 7 | 128 | 124 | 130 | 120 | 125 | 129 | 7,8125 | 8,0645 | 7,6923 | 8,3333 | 8 | 7,7519
CUARTO | 8 |  | 120 | 127 | 127 | 118 |  |  | 8,3333 | 7,874 | 7,874 | 8,4746
MESA | 1 | 118 | 127 | 117 | 127 | 122 | 109 | 8,4746 | 7,874 | 8,547 | 7,874 | 8,1967 | 9,1743
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

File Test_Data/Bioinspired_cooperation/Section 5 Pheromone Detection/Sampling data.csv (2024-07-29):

Location | Measurement | Avg Period (ms) | Avg Frecuency (Hz)
Cuarto | 1 | 2,6344 | 379,59
Cuarto | 2 | 2,617 | 382,12
Cuarto | 3 | 2,6324 | 379,88
Cuarto | 4 | 2,6229 | 381,26
Cuarto | 5 | 2,6489 | 377,51
Cuarto | 6 | 2,6565 | 376,43
Mesa | 1 | 2,7339 | 365,78
Mesa | 2 | 2,7453 | 364,26
Mesa | 3 | 2,7379 | 365,24
Mesa | 4 | 2,7498 | 363,67
Mesa | 5 | 2,7431 | 364,55
Mesa | 6 | 2,7392 | 365,07
Sala | 1 | 2,8522 | 350,6
Sala | 2 | 2,8584 | 349,85
Sala | 3 | 2,8387 | 352,27
Sala | 4 | 2,8429 | 351,75
Sala | 5 | 2,8625 | 349,34
Sala | 6 | 2,8465 | 351,31
 | Average | 2,74236 | 365,027
 | Std Dev | 0,09081 | 12,101

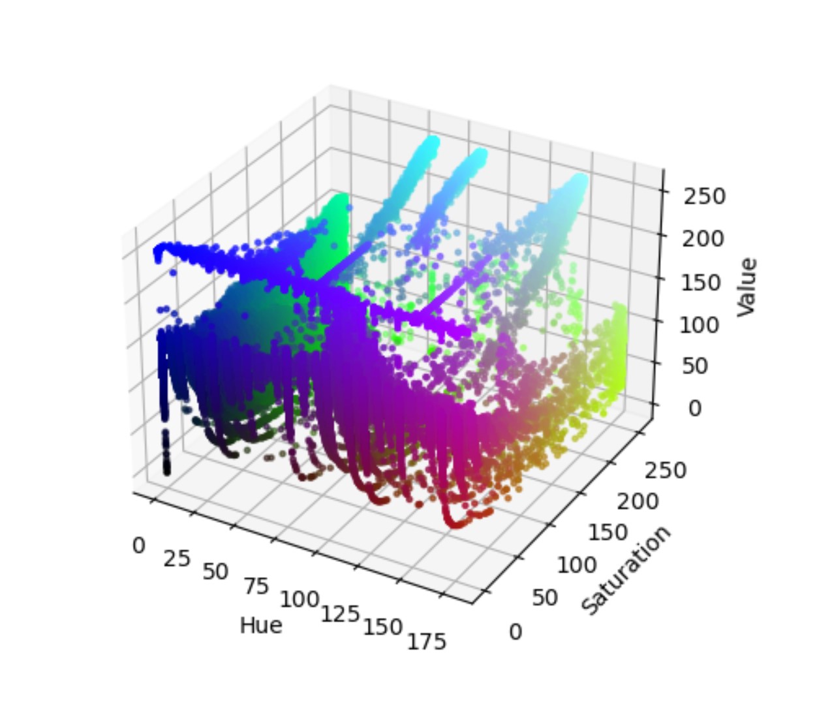
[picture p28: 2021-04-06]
Herramientas/Cámara/VALIDACION_ANTERIOR/Segmentación por color/Fotos antiguas/PruebaIdentificadoresColor HSV.jpg

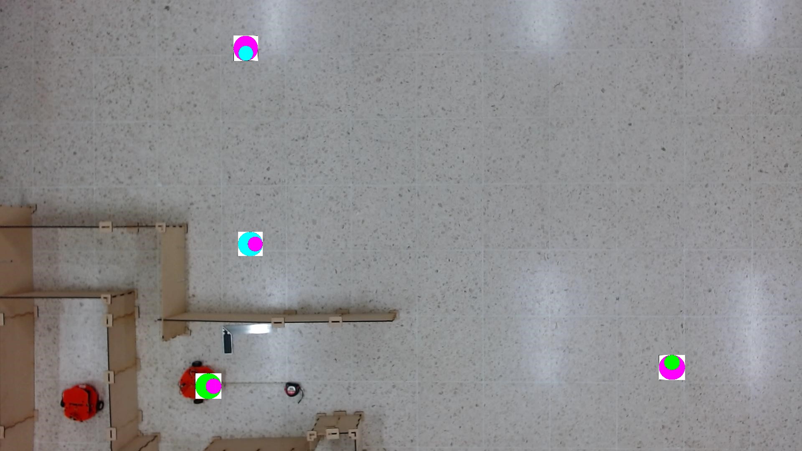
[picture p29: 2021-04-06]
Herramientas/Cámara/VALIDACION_ANTERIOR/Segmentación por color/Fotos antiguas/PruebaIdentificadoresColor.jpg

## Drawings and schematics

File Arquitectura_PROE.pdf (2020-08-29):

## Sistema de navegación

# PROYECTO PROE

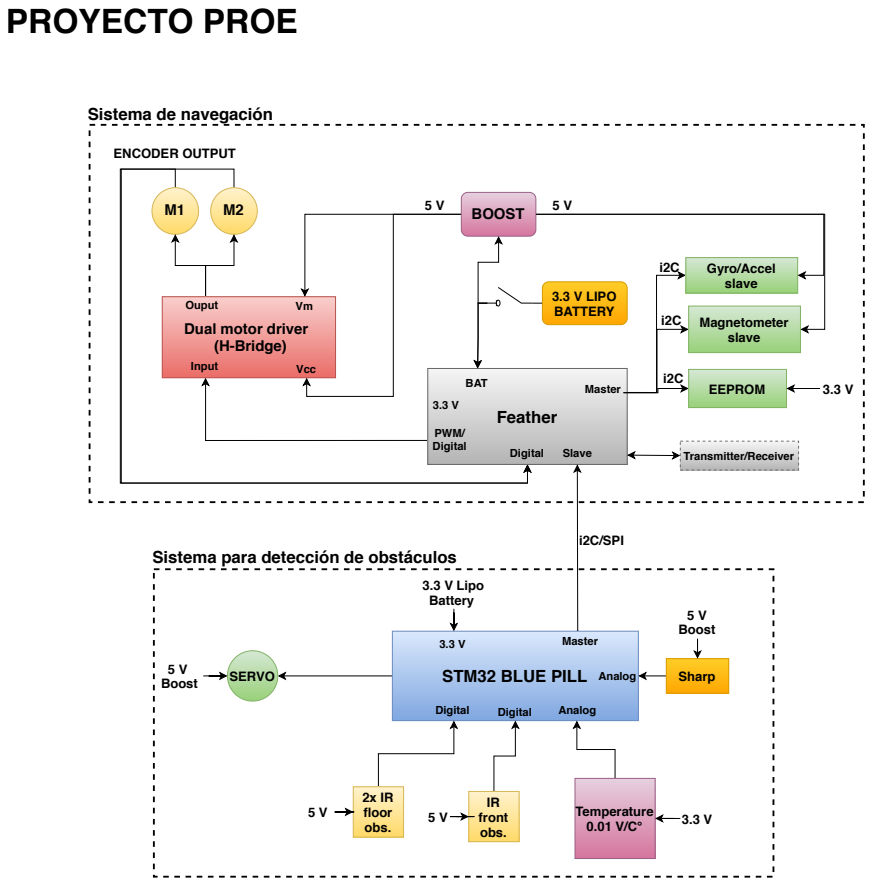
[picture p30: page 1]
Vcc; BOOST; 3.3 V LIPO BATTERY; Feather; BAT; Master; Slave; Transmitter/Receiver; Magnetometer slave; Gyro/Accel slave; PWM/ Digital; Input; ENCODER OUTPUT; Digital; STM32 BLUE PILL; Temperature 0.01 V/C°; 2x IR floor obs.; 3.3 V Lipo Battery; i2C/SPI; Analog; Sharp; 5 V Boost; IR front obs.; SERVO 5 V Boost; EEPROM

Ouput
Dual motor driver
(H-Bridge)

Sistema para detección de obstáculos

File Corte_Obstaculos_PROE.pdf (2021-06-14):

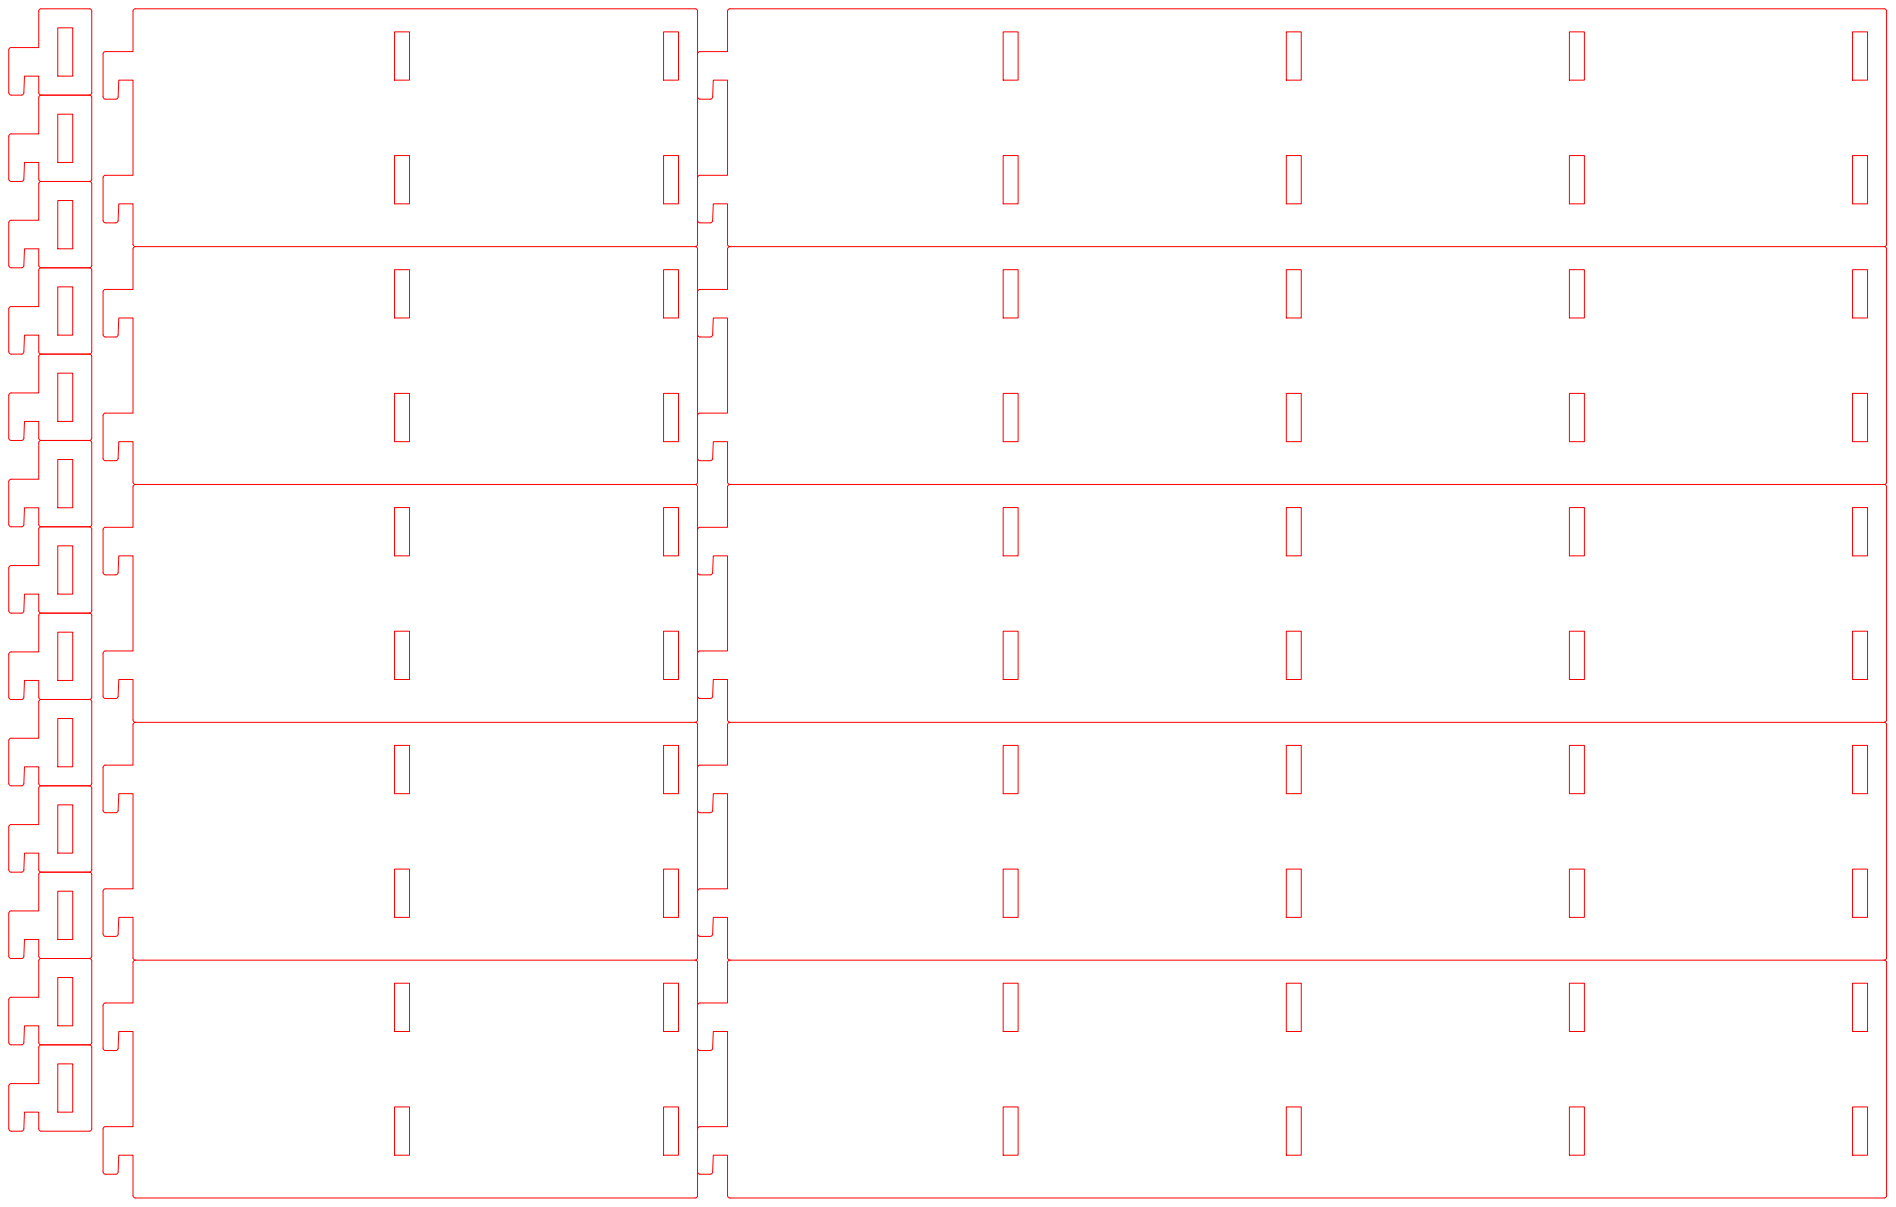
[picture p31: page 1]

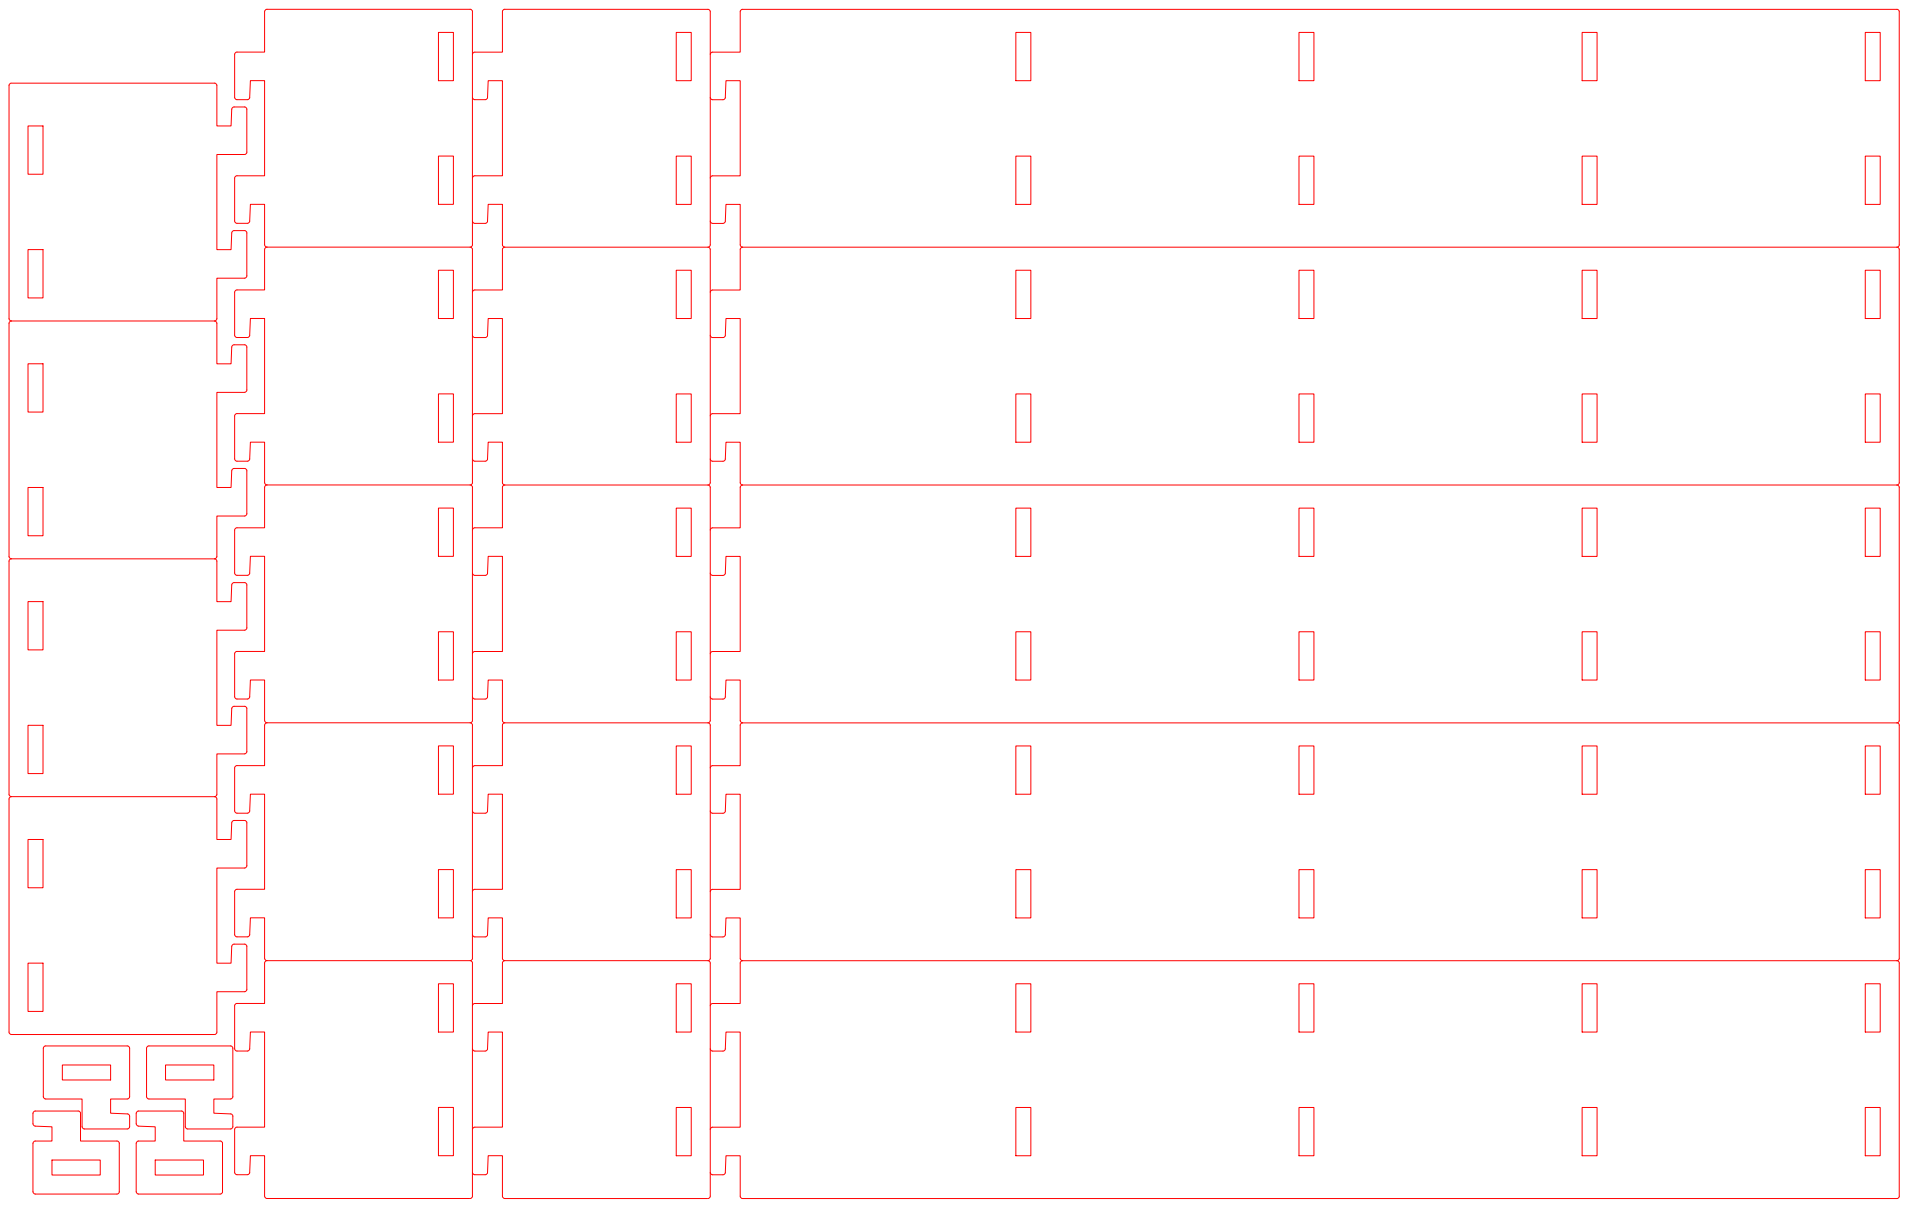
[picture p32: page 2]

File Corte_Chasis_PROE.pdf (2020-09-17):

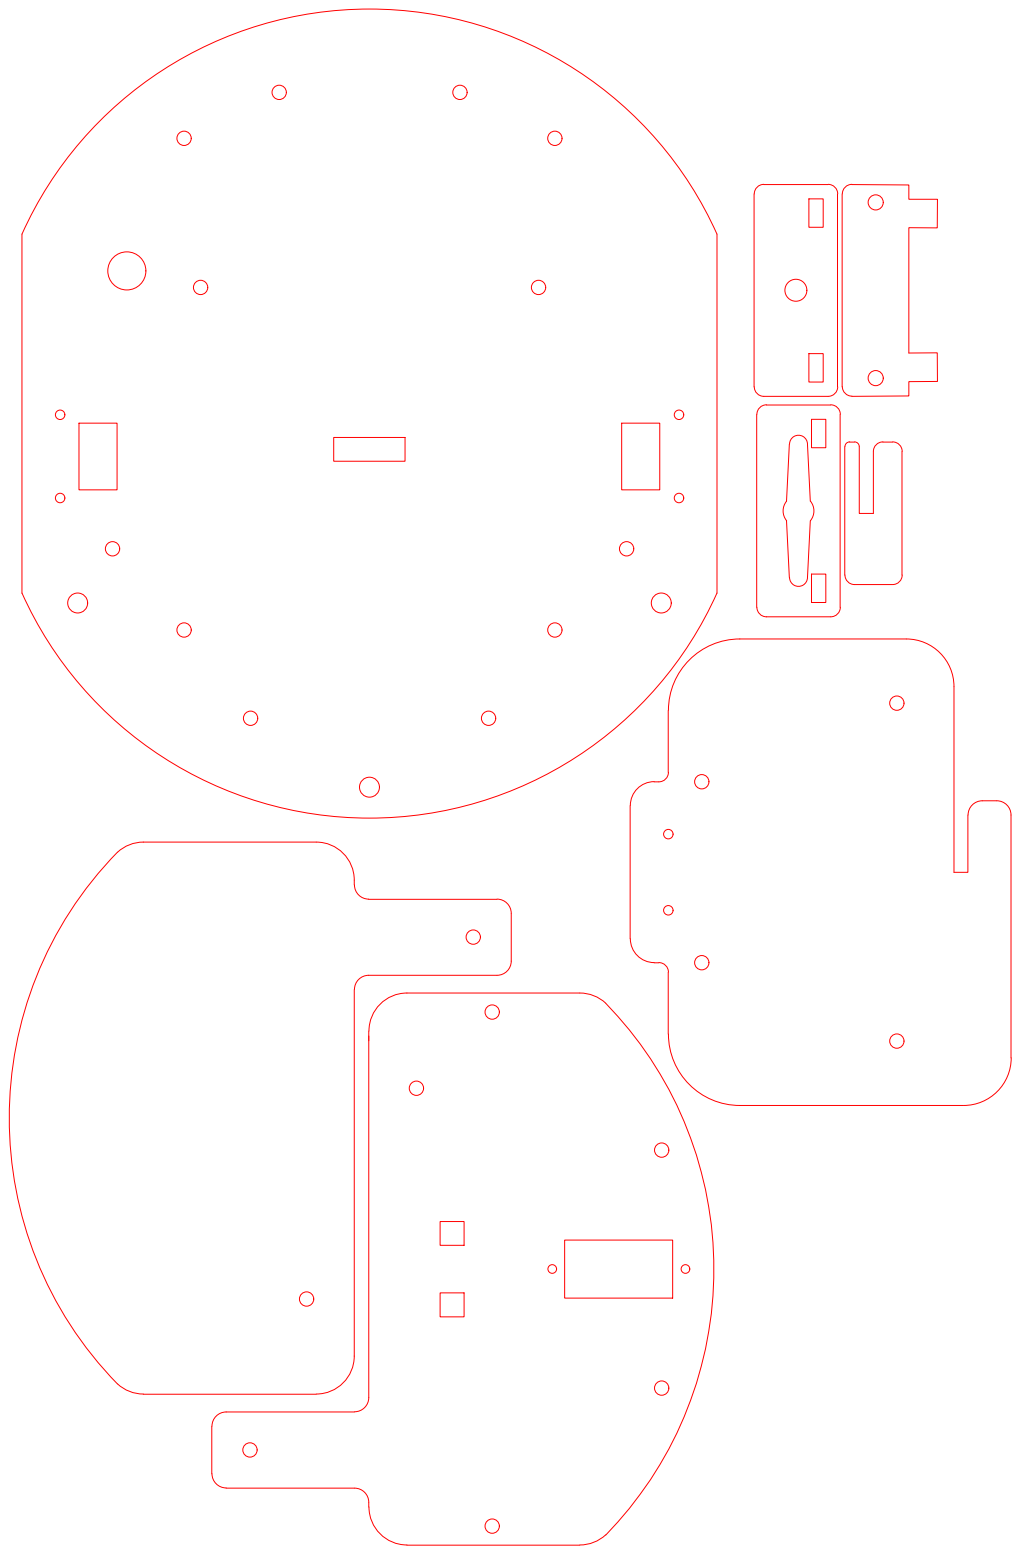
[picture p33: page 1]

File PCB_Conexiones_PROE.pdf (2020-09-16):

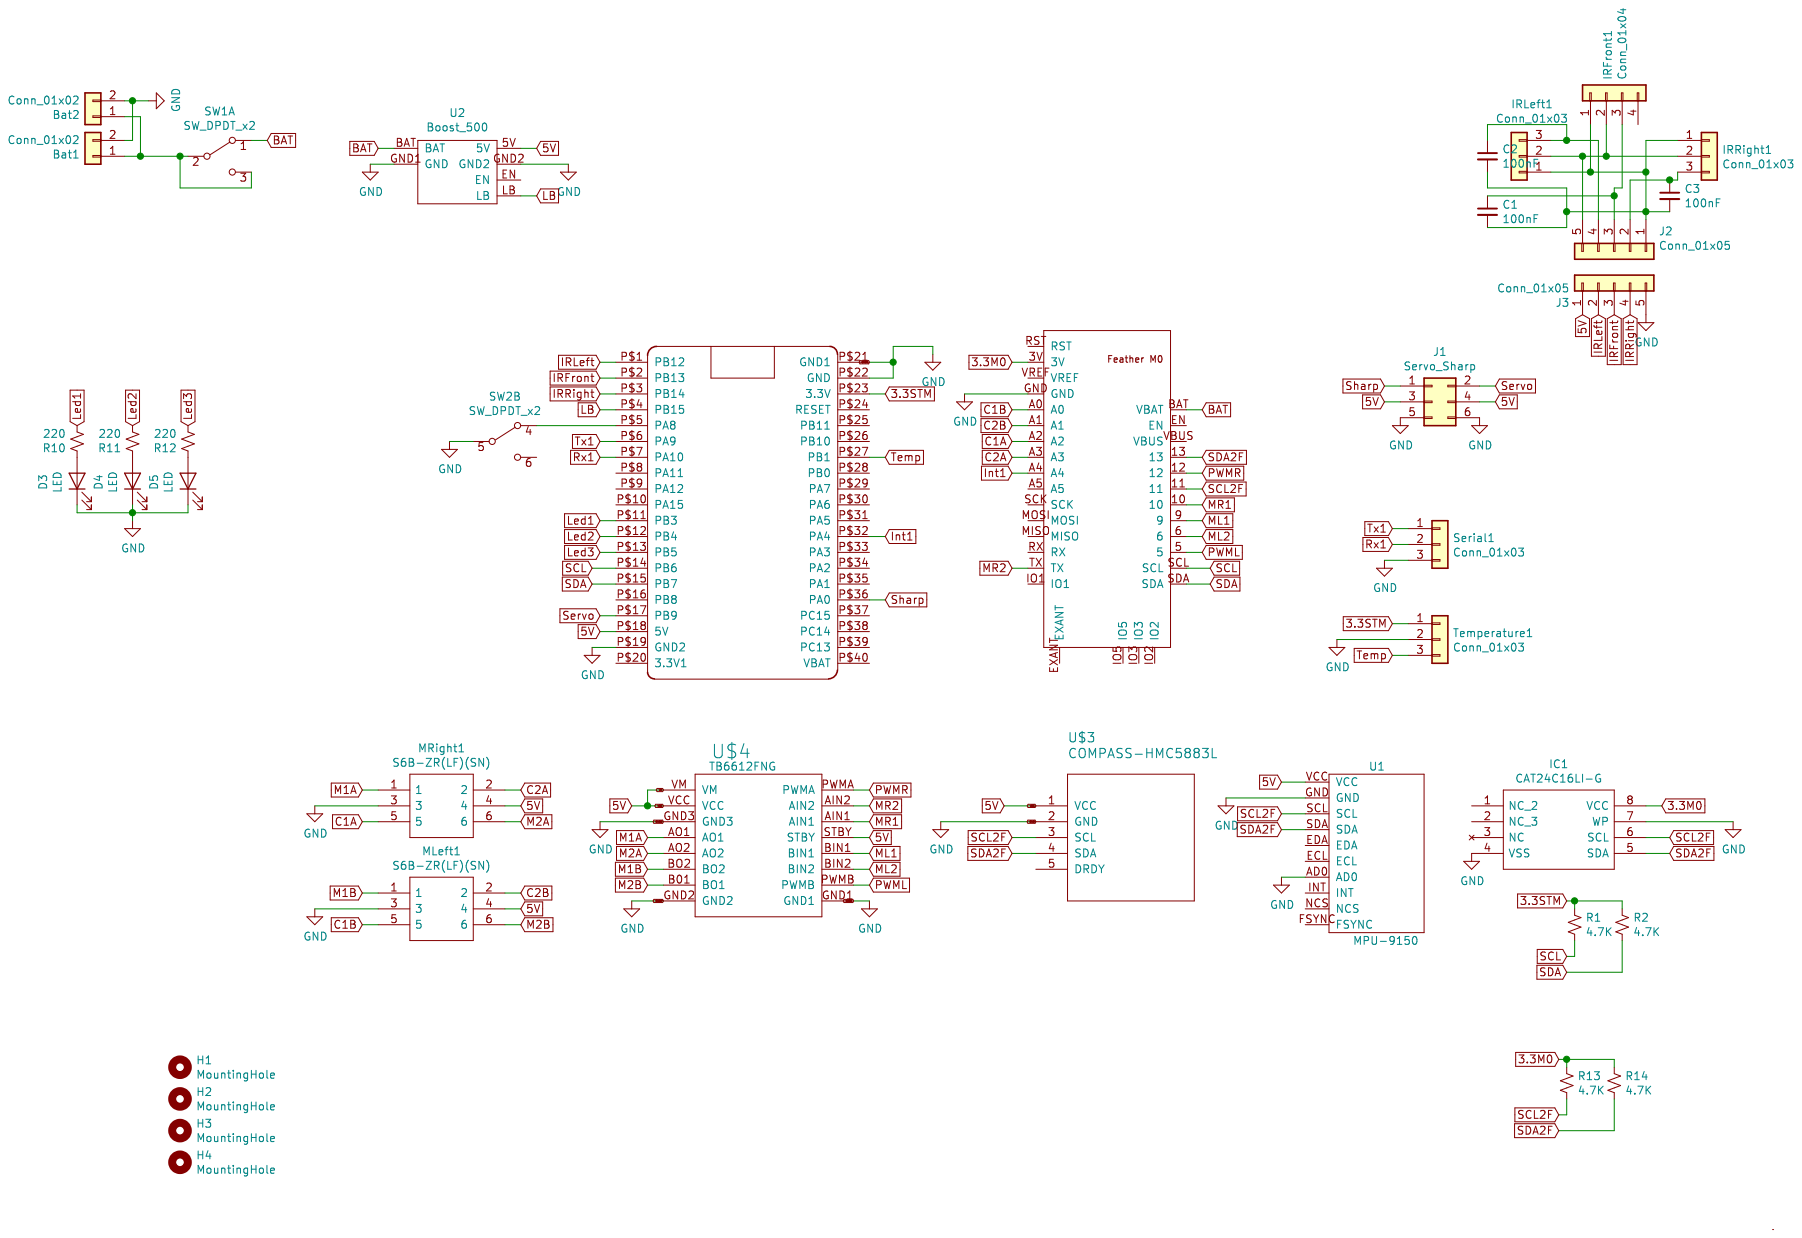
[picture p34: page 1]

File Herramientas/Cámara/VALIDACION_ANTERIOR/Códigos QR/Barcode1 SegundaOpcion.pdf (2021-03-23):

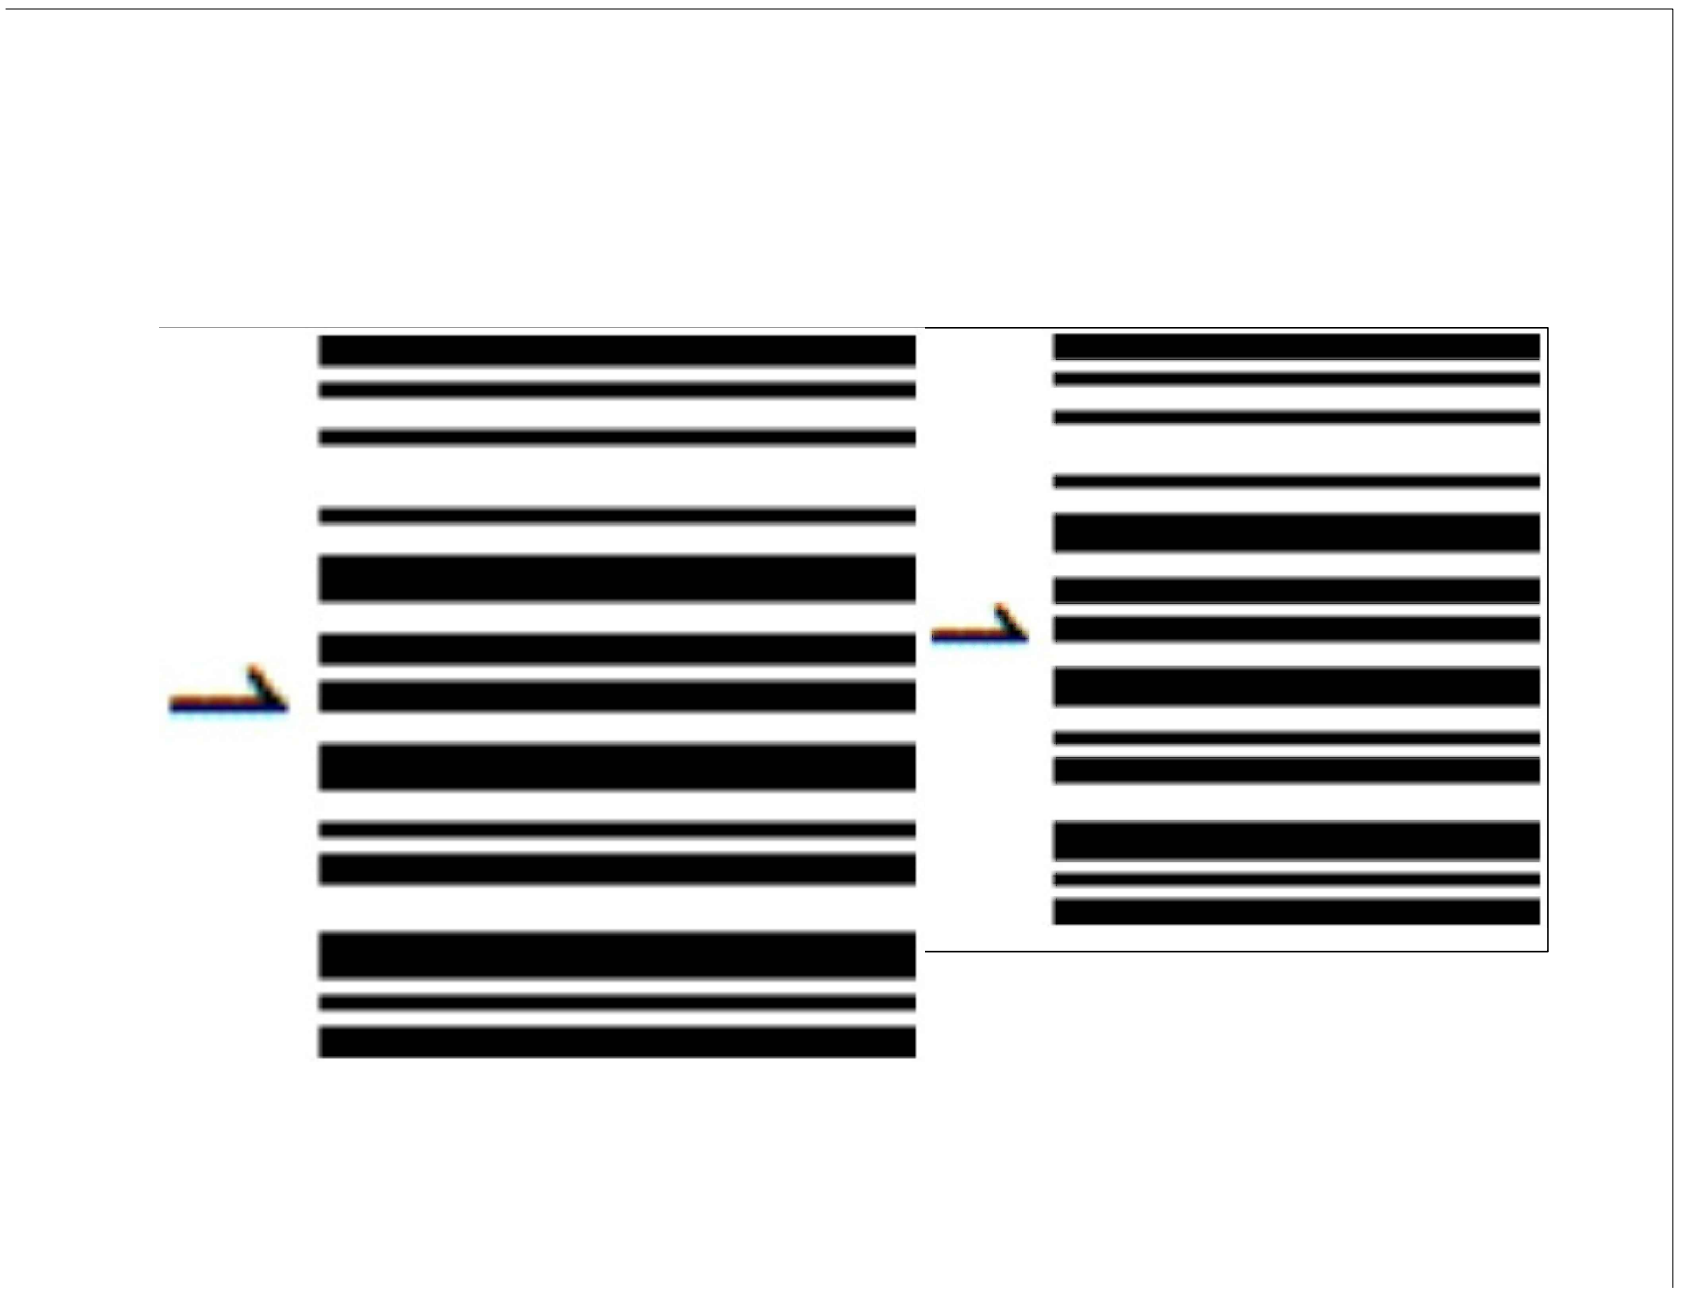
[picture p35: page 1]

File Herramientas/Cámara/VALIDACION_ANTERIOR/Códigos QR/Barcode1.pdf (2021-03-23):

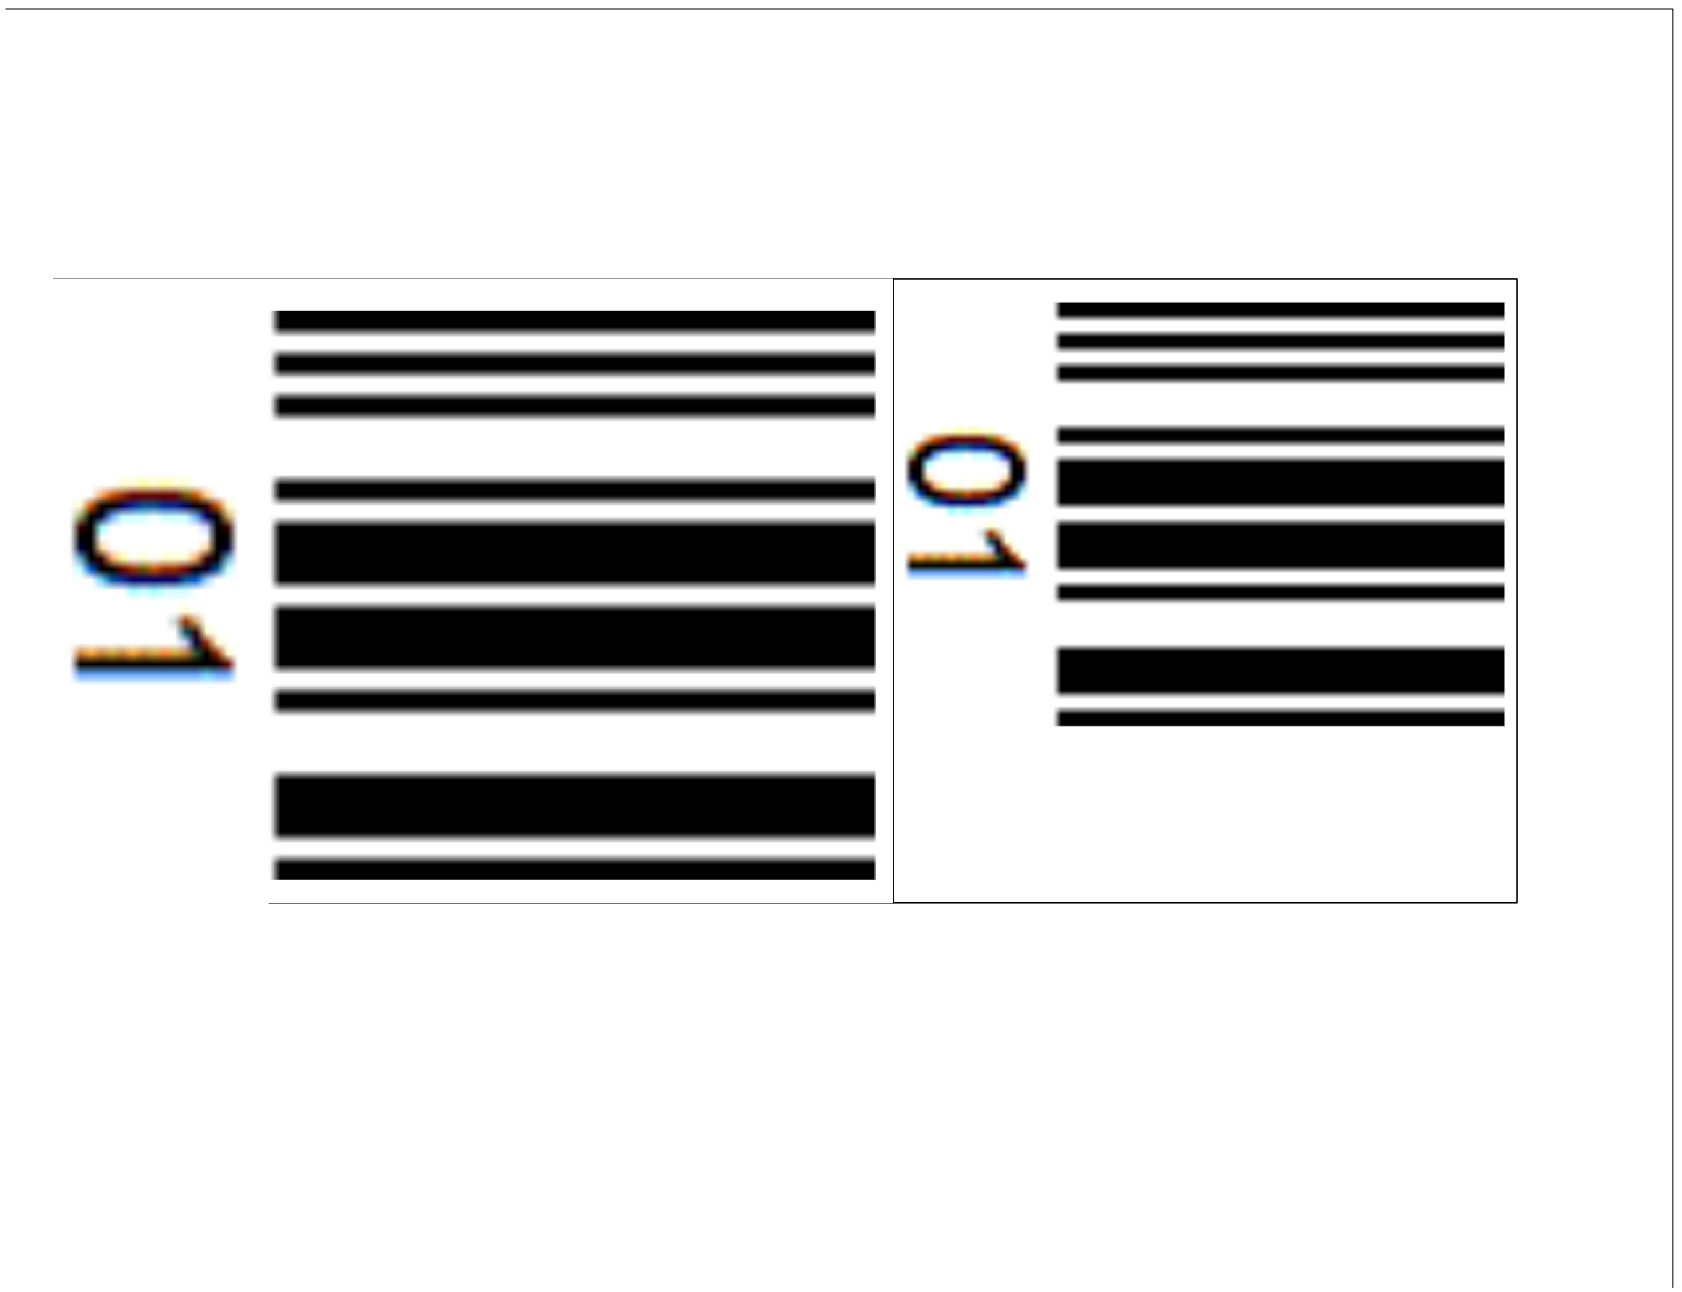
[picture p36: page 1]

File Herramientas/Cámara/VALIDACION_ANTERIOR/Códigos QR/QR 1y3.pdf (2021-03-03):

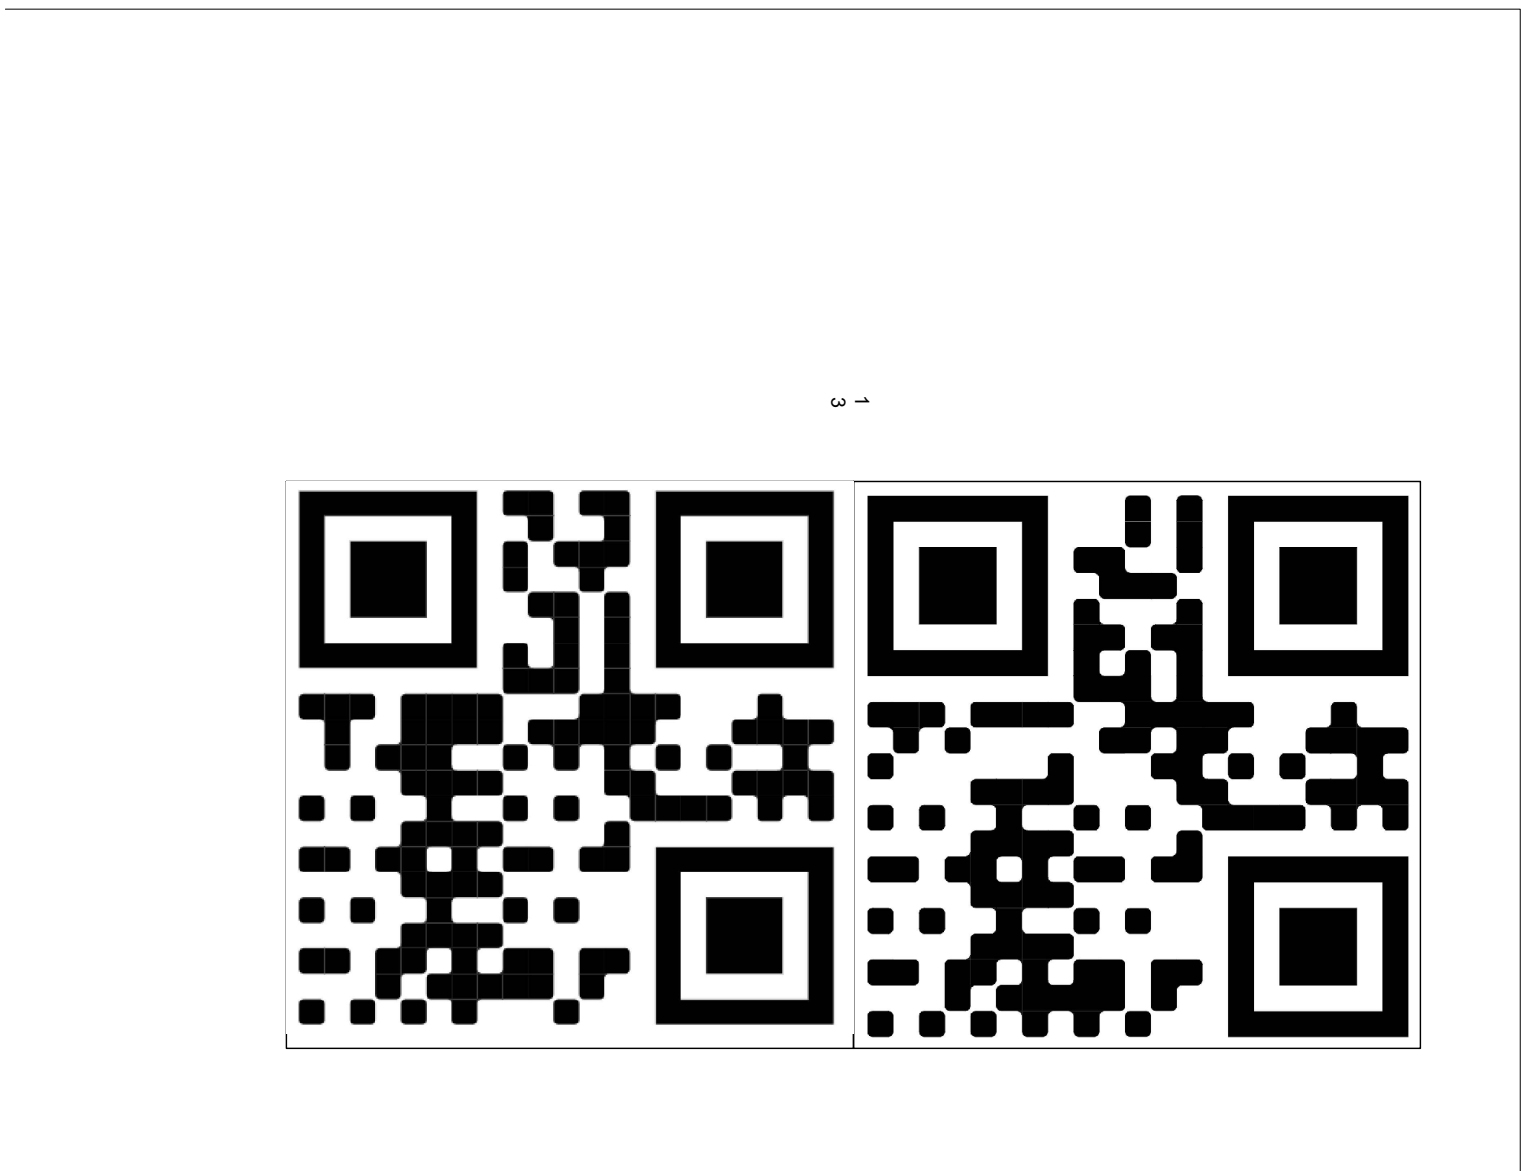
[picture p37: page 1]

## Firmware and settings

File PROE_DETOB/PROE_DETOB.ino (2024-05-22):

/** \file PROE_DETOB.ino
 * \author PROE
 * \link https://github.com/jcbrenes/PROE \endlink
 * \brief Código de detección de obstáculos
 * Usado en la placa Bluepill STM32
 *
 * Se encarga de la lectura de sensores y comunica cualquier evento mediante i2c al feather al que está conectado despues de notificarle mediante un pin adicional de interurpcion
 * Se usa el formato "x,y,z." donde "x" es el código del evento, "y" es el valor de lectura si aplica y "z" el angulo en caso del sensor Sharp.
 * Códigos de evento:
 *   1)Sensor Sharp
 *   2)IR frontal
 *   3)IR derecho
 *   4)IR izquierdo
 *   5)Temperatura
 *   6)Batería baja
 * Adicionalmente tiene tres salidas conectadas a leds para notificación y un switch extra 
 */

#include <Servo.h>
#include <Wire_slave.h>   //para usar el STM32 como secundario en el puerto I2C                   
//https://github.com/rogerclarkmelbourne/Arduino_STM32/tree/master/STM32F1/libraries/WireSlave 

/************ Serial Setup ***************/
#define debug 1

#if debug == 1
#define serialPrint(x) Serial1.print(x)
#define serialPrintln(x) Serial1.println(x)
#else
#define serialPrint(x)
#define serialPrintln(x)
#endif

Servo myServo;

//Declaración de pines//
#define irLeft PB12 //Sensor ir izquierda
#define irFrontal PB13 //Sensor ir frontal
#define irRight PB14 //Sensor ir derecha
#define lowBattery PB15 //Pin de batería baja del boost
#define interruptor PA8 //Interruptor adicional, usar pullup de software
#define led1 PB5 //Led adicional rojo
#define led2 PA3 //Led adicional amarillo
#define led3 PA5 //Led adicional azul
#define serv PB9 //Servo
#define temp PB1 //Sensor de temperatura
#define int1 PA4 //Pin de interrupción para el feather
#define sharp PA0 //Sharp (ir de distancia)

// Configuración inicial
bool distInicialListo = false;
int inicioFeatherListo = 0;
int offsetDistanciaInicial = 160; // Se agrega un offset de 16cm para la medición del sharp

//Constantes de configuración//
const float beta=0.1;  //Constante para el filtro, ajustar para cambiar el comportamiento
const int servoDelay=3; //Tiempo entre cada paso del servo en milisegundos
const float distanciaMinimaSharp=140; //Distancia mínima en milimetros para detección de obstáculos
const int debounceTime=400; //Debounce para sensor IR frontal
const float maxTemp=40; //Temperatura de detección de fuego
const int movimientoMaximo=180; //Maxima rotacion en grados realizada por el servo que rota el sharp

//Variables globales//
int angulo=0;
int anguloAnterior=0;
int lectura=0;
float distancia=5000; // Distancia medida por el sharp, valor inicial grande
float filtrado=0;
int cuentaBateria=0;
int sensorIRdetectado=0;
uint32_t millisAnterior=0;
int servoPos=0;
int incremento=1; //cantidad de grados que aumenta el servo en cada movimiento
bool ledON = false; 
int onTime= 300; //tiempo de encendido del LED en milisegundos
unsigned long millisLED=0;

int c=0; //Pulso de led para ver actividad del STM
unsigned long lastSend=0; //Almacena cuando se envio el ultimo obstaculo para evitar saturar la comunicación
const int sendDelay=100; //Tiempo minimo en ms entre cada envio de obstaculo (evita crash del stm)
char dato[10];
bool nuevoObstaculo = false;
unsigned long tiempoObstaculo=0; //Guarda en que momento se detecto el ultimo obstaculo
const int maxTiempoObstaculo=200; //Si no se atiende un obstaculo en 200ms se ignora

unsigned long lastPoll=0; //Almacena tiempo de ultima lectura de sensores IR
unsigned long pollingTime=100; //Tiempo minimo entre lectura de sonsores IR
int lastIR=0; //Ultimo sensor IR que se detecto, evita repetir mensajes

bool pausa = 0; //Sirve para hacer un delay cada vez que el servo del Sharp llegó a 0 o 180°
const int cambioDireccionDelay = 350; //Delay para que el servo cambie de dirección

void setup() {
  myServo.attach(serv,500,1600); //Une el objeto myServo al pin del servo (serv, min, max) valores en us para mover el servo a su posición minima y máxima (calibración)

  //Configuración de pines//
  pinMode(irFrontal, INPUT);
  pinMode(irLeft, INPUT);
  pinMode(irRight, INPUT);
  pinMode(interruptor, INPUT_PULLUP);
  pinMode(lowBattery, INPUT);
  pinMode(led1, OUTPUT);
  pinMode(led2, OUTPUT);
  pinMode(led3, OUTPUT);
  pinMode(temp, INPUT);
  pinMode(int1, OUTPUT);
  pinMode(sharp, INPUT);

  digitalWrite(int1,LOW); //Que el pin de int esté en bajo
  delay(100); //Algunos sensores capturan ruido al inicio, los delays es para evitar eso

  //Configuración de perifericos//
  Wire.begin(8);           //Inicia comunicación i2c como master
  Wire.onRequest(responderFeather);
  Serial1.begin(115200);  //Inicia la comunicación serial a 115200 baud
  Serial1.println("On");  //Enviar un "on" por el serial para confirmar que el setup se ejecutó correctamente

  servoPos = movimientoMaximo/2;
  myServo.write(servoPos); //Coloca el servo en el centro para confirmar alineación
  //myServo.writeMicroseconds(1500);
  revisarInterruptor();
  delay(100); //Algunos sensores capturan ruido al inicio, los delays es para evitar eso

  avizarDistancia(lecturaInicialSharp()); // Hace la lectura para la transformación de coordenadas
  serialPrintln("Lectura de distancia lista");
}
 
void loop() {
  if (distInicialListo){
    moverServo(); //Serial1.println("Servo");
    revisarSharp(); //Serial1.println("Sharp");
    pollingSensoresIR(); //Serial1.println("Poll");  //Leer sensores IR por polling
    revisarSensoresIR(); //Serial1.println("IR");
    revisarTemperatura(); //desactivado mientras no está soldado el sensor al PCB
    revisarBateria(); //Serial1.println("Bat");
    encenderLED(); //Serial1.println("LED"); //enciende un led si alguna función lo activó 
    actividad(); //Serial1.println("Actividad");//Parpadea led amarillo para confirmar actividad del stm
  }
}

/// \brief Realiza la lectura inicial de la distancia que está el robot.
/// \return La distancia filtrada después de 100 mediciones
int lecturaInicialSharp(){
    int contador = 0;
    while (contador < 100){
        lectura=analogRead(sharp);
        filtrado=filtrado-(beta*(filtrado-lectura)); //Filtro de media movil
        distancia=1274160*pow(filtrado,-1.174); //Regresión lineal de datos experimentales para obtener distancia en milimetros
        delay(50);
        contador += 1;
    }
    Serial1.println(distancia);
    return int(distancia + offsetDistanciaInicial);
}

/// \brief Crea el mensaje a ser enviado para la transformación de coordenadas e indica que está listo para transmitir
void avizarDistancia(int information){ //Prepara el paquete de datos con la información de obstaculo detectado    
  sprintf(dato, "%d.", information); //Genera un string para la transmisión
  nuevoObstaculo = true;
  digitalWrite(int1,HIGH); //Pulsar salida int1 para indicarle al feather que se detectó un obstaculo 
  delay(50);
  digitalWrite(int1,LOW);  
  delay(1000); //delay para que el STM no sature al feather con la misma interrupción
}

void moverServo(){ //Mueve el servo un valor determinado cada cierto tiempo
  //Al llegar a 0 o 180°, el servo espera cambioDireccionDelay milisegundos para comenzar a girar al otro lado
  if((millis() - millisAnterior) > cambioDireccionDelay && pausa == 1) {
    pausa = 0;
  }
  if((millis() - millisAnterior) > servoDelay && pausa == 0) {  //Se utiliza la función millis para evitar usar los delays
    millisAnterior = millis();
    servoPos += incremento;
    myServo.write(servoPos);
    angulo= movimientoMaximo/2 - servoPos; //se considera 0 grados justo al frente
    angulo=-angulo; //Posición de servo invertida en nuevo chasis
    if ((servoPos >= movimientoMaximo) || (servoPos <= 0)){ // se terminó el semiciclo, se invierte la dirección
      incremento = -incremento;
      pausa = 1;
    }
  }
}

void encenderLED(){ //Se encarga de encender el LED por un tiempo determinado. Se utiliza la función millis para evitar usar los delays
  if(ledON){ //enciende el LED
    digitalWrite(led3,HIGH); 
    millisLED = millis();
    ledON = false; 
  }
  if((millis() - millisLED) > onTime) {  //Se apaga el LED luego de un rato
    digitalWrite(led3,LOW); 
  }
}

void revisarSharp(){ //Revisa el valor del sensor Sharp  
  lectura=analogRead(sharp);
  filtrado=filtrado-(beta*(filtrado-lectura)); //Filtro de media movil
  distancia=1274160*pow(filtrado,-1.174); //Regresión lineal de datos experimentales para obtener distancia en milimetros
  //Serial1.println(int(distancia));
  if ((distancia<distanciaMinimaSharp) && (angulo!=anguloAnterior)){ //revisa distancia umbral y que solo se haga un envío por cada ángulo
    crearMensaje(1,int(distancia),angulo); //Enviar obstaculo tipo 1 con distancia en cm y angulo
  }
  anguloAnterior=angulo;
}

void revisarTemperatura(){ //Lectura del sensor de temperatura
  float lectura = analogRead(temp);
  float temperatura = (0.08394*lectura)-54.162; //Formula extraida de la hoja de datos del sensor
  serialPrint(lectura);serialPrint(' ');serialPrintln(temperatura);
  if(temperatura>maxTemp){ //Valor máximo de temperatura aceptable
    int i = int(temperatura);
    crearMensaje(5,i,90); //Se pone angulo 90 para que no crea que es un obstáculo frontal
    //Serial1.println("T");
  }
}

void revisarBateria(){ //Revisar la batería cada 20 ciclos del loop, codigo 6
  if(!digitalRead(lowBattery)){ //Batería baja = pin bajo
    cuentaBateria++;
    if(cuentaBateria>=10000){ //Si la bateria esta baja enviar advertencia cada 10000 ciclos del loop principal
      crearMensaje(6,0,90);
      digitalWrite(led1,HIGH); //Encender led rojo si la batería está baja
      ledON=true;
      onTime=300;
      cuentaBateria=0;
    }
  }
}

void pollingSensoresIR(){ //Lectura de sensores IR por polling, prioridad al frontal
  if((millis() - lastPoll) > pollingTime){
    if(!digitalRead(irFrontal)){
      sensorIRdetectado=2;
    }
  
    else if(digitalRead(irRight)){
      sensorIRdetectado=3;
    }
  
    else if(digitalRead(irLeft)){
      sensorIRdetectado=4;
    }
  
    else{}

    lastPoll = millis();
  }
}

void revisarSensoresIR(){ //Revisa si la variable de sensores IR cambio de estado en un interupción, en ese caso envía el dato
//Esto es porque los serial y wire dentro de interrupciones dan problema

  switch (sensorIRdetectado) {
    case 0:    // no se ha detectado nada
      break;
    case 2:    // sensor IR frontal
      crearMensaje(2,0,0);
      sensorIRdetectado=0;
      //Serial1.print("F ");
      break;
    case 3:    // sensor IR inferior derecho
      crearMensaje(3,0,0);
      sensorIRdetectado=0;
      //Serial1.print("R ");
      break;
    case 4:    // sensor IR inferior izquierdo
      crearMensaje(4,0,0);
      sensorIRdetectado=0;
      //Serial1.print("L ");
      break;
  }
}

void actividad(){
  if(c>5000){//Parpadea led amarillo para señalar actividad del stm
    digitalWrite(led2,!digitalRead(led2));
    c=0;
  }
  else{
    c=c+1;
  }
}

void revisarInterruptor(){
  if(!digitalRead(interruptor)){
    digitalWrite(led1, HIGH);
    crearMensaje(-1,0,0);
  }
  else{
    digitalWrite(led1, LOW);
  }
}

void crearMensaje(int caso, int distancia, int angulo){ //Prepara el paquete de datos con la información de obstaculo detectado    
  sprintf(dato, "%d,%d,%d.", caso, distancia, angulo); //Genera un string para la transmisión
  nuevoObstaculo = true;
  tiempoObstaculo = millis();
  ledON=true;
  onTime=300;

  //Solo si el obstáculo está en frente activa el pin de interrupción para el feather (modo crítico)
  if (abs(angulo)<=40){
    digitalWrite(int1,HIGH); //Pulsar salida int1 para indicarle al feather que se detectó un obstaculo 
    digitalWrite(int1,LOW);  
    delay(1000); //delay para que el STM no sature al feather con la misma interrupción
  }
}

void responderFeather(){ 
  if (nuevoObstaculo){ //Evita enviar el mismo obstaculo dos veces
    Wire.write(dato);  //Envia el valor al master
    memset(dato,0,10); //Resetea el valor almacenado en dato, para evitar que se envie mas
    nuevoObstaculo = false;
    // El feather debe avisar que terminó el proceso de arranque, luego la operación es normal
    if (inicioFeatherListo == 2 && distInicialListo == false){
      distInicialListo = true;
    }else{
      inicioFeatherListo += 1;
      nuevoObstaculo = true;
    }
  }else{
    Wire.write(""); 
  }
}

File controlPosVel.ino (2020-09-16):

//Código principal para el proyecto PROE
//https://github.com/jcbrenes/PROE

#include<Wire.h> //Bilbioteca para la comunicacion I2C

//constantes del robot empleado
const int tiempoMuestreo=10000; //unidades: micro segundos
const float pulsosPorRev=206.0; //cantidad de pulsos de una única salida
const int factorEncoder=4; //cantidad de tipos de pulsos que se están detectando (juego entre las 2 salidas del encoder)
const float circunferenciaRueda=139.5;//Circunferencia de la rueda = 139.5mm 
const float pulsosPorMilimetro=((float)factorEncoder*pulsosPorRev)/circunferenciaRueda; 
const float distanciaCentroARueda=87.5;// Radio de giro del carro, es la distancia en mm entre el centro y una rueda. 
const float conversionMicroSaMin=1/(60 * 1000000);// factor de conversion microsegundo (unidades del tiempo muestreo) a minuto
const float conversionMicroSaSDiv=1000000;// factor de conversion microsegundo (unidades del tiempo muestreo) a segundo
const float tiempoMuestreoS= (float)tiempoMuestreo/conversionMicroSaSDiv;

//constantes para control PID de velocidad (están unidas con la constante de tiempo por simplificación de la ecuación)
const float velRequerida=150; //unidades mm/s
const float KpVel=2; //constante control proporcional
const float KiVel=20.0 * tiempoMuestreoS; //constante control integral
const float KdVel=0.01 / tiempoMuestreoS ; //constante control derivativo
//constantes para control PID de giro 
const float KpGiro=2; //constante control proporcional
const float KiGiro=20.0 * tiempoMuestreoS;//constante control integral
const float KdGiro=0.08 / tiempoMuestreoS; //constante control derivativo

//Constantes para la implementación del control PID real
const int errorMinIntegral=-250;
const int errorMaxIntegral=250;
const int limiteSuperiorCicloTrabajoVelocidad=200;
const int limiteInferiorCicloTrabajoVelocidad=0;
const int limiteSuperiorCicloTrabajoGiro=200;
const int limiteInferiorCicloTrabajoGiro=-200;
const int cicloTrabajoMinimo= 20;
const int minCiclosEstacionario= 20;

//Configuración de pines de salida para conexión con el Puente H
const int PWMA = 12; //Control velocidad izquierdo
const int AIN1 = 10; //Dirección 1 rueda izquierda 
const int AIN2 = 1; //Dirección 2 rueda izquierda 
const int PWMB = 5;  //Control velocidad derecha
const int BIN1 = 9;  //Dirección 1 rueda derecha
const int BIN2 = 6;  //Dirección 2 rueda derecha

//Configuración de los pines para la conexión con los Encoders
const int ENC_DER_C1 =  A0; //Encoders rueda derecha
const int ENC_DER_C2 =  A1;
const int ENC_IZQ_C1 =  A2; //Encoders rueda izquierda
const int ENC_IZQ_C2 =  A3;

//Configuracion de los pines de interrupcion de Obstáculos
const int INT_OBSTACULO = A4;

//Almacenamiento de datos de obstáculos
const int longitudArregloObstaculos = 200;

//VARIABLES GLOBALES

//Variables para la máquina de estados principal
enum PosiblesEstados {AVANCE=0, GIRE_DERECHA, GIRE_IZQUIERDA,ESCOGER_DIRECCION,GIRO, NADA};
char *PosEstados[] = {"AVANCE", "GIRE_DERECHA", "GIRE_IZQUIERDA","ESCOGER_DIRECCION","GIRO", "NADA"};
PosiblesEstados estado = NADA; //AVANCE;

//variable que almacena el tiempo del último ciclo de muestreo
long tiempoActual=0;

//contadores de pulsos del encoder
int contPulsosDerecha=0;
int contPulsosIzquierda=0;
int contPulsosDerPasado=0;
int contPulsosIzqPasado=0;

//Variables que almacenan el desplazamiento angular de cada rueda
float posActualRuedaDerecha=0.0;
float posActualRuedaIzquierda=0.0;

//Variables del valor de velocidad en cada rueda
float velActualDerecha=0.0;
float velActualIzquierda=0.0;

//Valores acumulados para uso en las ecuaciones de control
//Para Giro
float errorAnteriorGiroDer=0;
float errorAnteriorGiroIzq=0;
float sumErrorGiroDer=0;
float sumErrorGiroIzq=0;
int contCiclosEstacionarioGiro=0;
//Para Velocidad
float errorAnteriorVelDer=0;
float errorAnteriorVelIzq=0;
float sumErrorVelDer=0;
float sumErrorVelIzq=0;

//Variables para las interrupciones de los encoders
byte estadoEncoderDer=1; 
byte estadoEncoderIzq=1;

//Variables para el algoritmo de exploracion
bool giroAnteriorIzquierda=0;
bool giroAnteriorDerecha=0;
int direccionDeseada=1;//random(1,5);//asigna direccion N,S,E,O 
int direccionActual=1; // 1=N, 2=E, 3=S, 4=O
bool giroTerminado=1;
bool detectaObjeto=0;
int anguloGiro = 90;
bool direccionAdelanteDisponible=1;
bool direccionIzquierdaDisponible=1;
bool direccionDerechaDisponible=1;
int opcionGiro=0;// puede tener 3 valores, 1=Izquierda 2=Adelante, 3=Derecha
bool asignarDireccionDeseada=0;

//Variables para la comunicaciónI2C
//TwoWire myWire(&sercom1, 11, 13);
int datosSensores[longitudArregloObstaculos][3]; //Arreglo que almacena la información de obstáculos de los sensores (tipo sensor, distancia, ángulo)
int ultimoObstaculo=-1; //Se inicializa en -1 porque la función de guardar aumenta en 1 el índice


void setup() {
  pinMode(PWMA, OUTPUT);
  pinMode(AIN1, OUTPUT);
  pinMode(AIN2, OUTPUT);
  pinMode(PWMB, OUTPUT);
  pinMode(BIN1, OUTPUT);
  pinMode(BIN2, OUTPUT);
  pinMode(INT_OBSTACULO, INPUT_PULLUP);
  pinMode(13,OUTPUT); //LED del feather
  attachInterrupt(ENC_DER_C1, PulsosRuedaDerechaC1,CHANGE);  //conectado el contador C1 rueda derecha
  attachInterrupt(ENC_DER_C2, PulsosRuedaDerechaC2,CHANGE); 
  attachInterrupt(ENC_IZQ_C1, PulsosRuedaIzquierdaC1,CHANGE);  //conectado el contador C1 rueda izquierda
  attachInterrupt(ENC_IZQ_C2, PulsosRuedaIzquierdaC2,CHANGE);
  //attachInterrupt(digitalPinToInterrupt(INT_OBSTACULO), DeteccionObjeto,FALLING);
  Serial.begin(9600);
  tiempoActual=micros(); //para temporización de los ciclos
  randomSeed(analogRead(A5)); //Para el algoritmo de exploración
  //direccionDeseada=random(1,5);//asigna direccion N,S,E,O
  Wire.begin(42); // En el puerto I2c se asigna esta dirección como esclavo
  Wire.onReceive(recibirI2C);
  //Wire.onRequest(requestEvent); // Se necesitan estas funciones porque el feather es el esclavo
  delay(3000);
}
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

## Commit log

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2019-02-14 Add files via upload
    Archivos de SolidWorks
    [Boost.SLDPRT, Ensamblaje1.SLDASM, IMU.SLDPRT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]
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2019-02-15 Add files via upload
    Se realiza la implementación del control de velocidad para ambas ruedas, se requiere ajustar los valores de las constantes de control
2019-02-15 Add files via upload
    Implementación control PID para las ruedas del carro, está pendiente definir si ambas ruedas debe controlarse por separado o si una rueda debe seguir a la otra, sin embargo se observan oscilaciones y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
2019-02-15 Add files via upload
    Versión comentada. Se le cambió el nombre a algunas variables.
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2019-02-22 Update controlVel.ino
    Se agregó la variación en tiempo dependiendo de los grados que se requiere girar.
2019-04-05 Add files via upload
    Contiene la programación del control del giro por posición.
2019-06-25 Add files via upload
    Archivo utilizado en la validación del giro de los agentes.
2019-07-31 Se agrega el Arduino Pos Vel
    Archivo de Arduino que integra control PID de posición y de velocidad
2019-08-08 Update controlPosVel.ino
    Revisé el código y la función AsignarDirecciónDeseada la quité porque no era necesaria, entonces quedó sólo la variable asignarDireccionDeseada. Aparte de eso para hacerlo funcionar había que editar 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
2019-08-14 Update controlPosVel.ino
    Bug del avanzar corregido
    [controlPosVel.ino]
2019-08-28 Corrección constante máximas
    Correccion de PWM máximos, error máximo, Kp de giro, y PWM mímino
    [controlPosVel.ino]
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2020-08-03 Actualización de pines para PCB
    Se cambia la asignación de pines de los motores para calzar con los del PCB. Se actualiza la distancia del centro del carro a la rueda.
2020-08-12 Major update al código
    Se sacan funcioner serial y wire de las interrupciones
    Se cambia el movimiento del servo con delay a uso de millis
    Se actualiza la distancia mínima del sharp, el ángulo máximo del servo y el valor de tiempo entre movimientos
2020-08-28 Update Stm32_combo_v2.ino
    Se ajusto la función de prender los LEDs para que no use Delay. Se cambió el monitor de batería para que solo avise con el LED.
2020-08-29 Add files via upload
    Diagrama de la arquitectura del sistema electrónico del robot
2020-09-16 Update controlPosVel.ino
    Se le agrega la rutina para recibir por el puerto I2C #1 la información proveniente del STM respecto a obstáculos y almacenarla en una arreglo.
    [controlPosVel.ino]
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2020-09-23 Update PROE_LOCOM.ino
    Cambio en longitud del arreglo de obstáculos
    [PROE_LOCOM.ino]
2020-09-23 Create Chasis PROE.dwg
    [Chasis PROE.dwg]
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2020-09-30 Update PROE_LOCOM.ino
    Se corrige actualización de la pose, tanto en ubicación como ángulo.
    [PROE_LOCOM.ino]
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2020-10-21 Modificaciones al archivo validacion
    Avance de las modificaciones y comentarios adicionales sobre el archivo de validacion. Actualmente, un error persiste y continua en estudio
2020-10-21 modificaciones validacion
    se continua buscando cómo corregir el error
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2020-11-04 Prueba correccion error
    Se intento con un nuevo set de calibracion y se corrio linea a linea el programa hasta encontrar la fuente del error: version, por lo que de ahora en adelante se trabajara con R2018a en lugar de R2014
2020-11-10 Avance corrección errores
    Se suprimieron 2 errores. Ahora deben tomarse nuevas imágenes ya que no está detectando los círculos de forma adecuada
2020-11-17 Prueba Desplazamiento/Rotacion
    Se actualizó parte del código a la versión matlab R2018a, se realizó una serie de capturas de imágenes con el fin de realizar pruebas de traslación y rotación. Se corrigieron errores anteriores respecto al uso de funciones de matlab. Los resultados de traslación y rotación fueron verificados y son satisfactorios. Únicamente resta revisar el código de la línea 172 en adelante, que según explica Sebastián es una parte que ocupaba Carlos, pero para nuestros objetivos, es necesario revisarla.
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2021-03-01 Avance códigos QR
    Se requiere imprimir los 3 pdf que están en la carpeta de Códigos QR, esto para tomar fotos donde salgan robots con su respectivo QR, y que en alguna zona de la imagen esté el patrón (para poder quit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
    [ExportadorCodigosTamañoReal.dwg]
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2021-03-09 Avance de pruebas de QR, OCR e Identificador Modificado
    Se adjunta una versión mejorada del reconocimiento de círculos de ubicación de cada robot móvil, mediante un nuevo identificador. El código QR no es identificable a la altura de trabajo actual. El re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
    [ExportadorCodigosTamañoReal.dwg]
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2021-03-12 Arreglar conflicto
    [ExportadorCodigosTamañoReal.dwg]
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2021-03-18 Revert "Nuevo archivo con cosas por hacer"
    This reverts commit f2811b7f7bd3ad318d121660427adcb61a6cd1bd.
    [PROE_LOCOM.ino]
2021-03-18 Revert "Revert "Nuevo archivo con cosas por hacer""
    This reverts commit 769ace128a2a6c421a1bf46ef9549b220d9d49dc.
    [PROE_LOCOM.ino]
2021-03-22 Avance Diferenciación de Robots
    Dado que la herramienta de lectura de códigos de barra y códigos QR pertenece a la biblioteca de Visión por Computador, en su versión R2020a y posterior, no es accesible para la versión 2018 con la q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
    [ExportadorCodigosTamañoReal.dwg]
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2021-03-24 Update PROE_DETOB.ino
    Agregado sendDelay que evita que se envien datos de obstaculos muy seguido, la idea es evitar bug que detiene el robot.
    [PROE_DETOB.ino]
2021-04-05 Avance Segmentación por Color
    Se generó un conjunto de combinaciones de identificadores de colores que resalten del fondo del espacio imagen. Se inició el código en Python, tomando como base https://realpython.com/python-opencv-c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
    [ExportadorCodigosTamañoReal.dwg]
2021-04-06 Update PROE_LOCOM.ino
    Se corrigieron errores del último commit que impedían compilar. Algunos brakets de más y un estado repetido en el Loop.
    [PROE_LOCOM.ino]
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2021-04-19 Ajuste de máscaras de 6 colores distintos
    Se ajustaron los rangos de detección para los colores cyan, magenta, verde, azul, rojo y amarillo. Con esto, ya se tienen las máscaras para que cada imagen quede solo con el color necesario. Se deter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
    [ExportadorCodigosTamañoReal.dwg]
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2021-05-05 Create Chasís PROE 2.dwg
    [Chasís PROE 2.dwg]
2021-05-07 Actualización de nuevo chasís
    [Chasis PROE.dwg, Chasís PROE.dwg]
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2021-05-19 Correccion crash STM
    DETOB: sensores IR cambiados a polling, comunicación con feather cambiada a pollign controlado por el feather.
    LOCOM: agregado calculo de unbicacion real basado en distancia y angulo del magnetometro, funcion crearobstaculo agrega objeto obstaculo a la lista con los valores que se le envian permite agregar obstaculos 0 al final de cada avance completado sin obstaculos. RevisarSTM llama al STM para que pase los obstaculos detectados, encoders con interrupcion con factor de 2
    [PROE_DETOB.ino, PROE_LOCOM.ino]
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2021-05-31 Archivo para chasís en dxf
    [Chasís PROE.dxf]
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2021-06-08 Avance Seguimiento de Robots SIN ZOOM
    Se modificaron los parámetros para el seguimiento de los robots según un vídeo ingresado por el usuario, el cual NO tiene zoom. Se realizaron cambios a las implementaciones de dilatación de contornos debido al cambio en el zoom de la cámara. Se tuvo una reunión con la profesora Rebeca para mostrarle el avance, parámetros que se pueden cambiar, archivo y formato de salida. Queda pendiente terminar de ajustar el recorrido de los robots identificados que está dando error al realizar el cambio de zoom, además, se pidió por parte de la profesora incorporar en las primeras líneas del código la posición inicial de cada robot. El seguimiento del pre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
2021-06-13 Nuevo corte de obstaculos
    Nueva versión del escenario de 10cm de alto apropiada para la nueva versión del chasis
    [Obstaculos_PROE.dwg]
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2021-06-15 Obstaculos en formato dxf
    [Obstaculos_PROE.dwg, Obstaculos_PROE.dxf]
2021-06-25 Nuevo chasís con lateral actualizado
    [Chasís PROE.dwg, Chasís PROE.dxf]
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2022-03-03 Comunicación iddentificadores
    Se agregan los códigos para hacer la comunicación por medio de identificadores utilizando la liberia de RadioHead.
    Me falta agregar mejores comentarios al código, por el momento existe un problema en la comunicación, los esclavos siempre se deben encender antes del master, si no se hace de esta forma no hay comunicación.
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2022-04-01 Sincronización RadioHead sin modificar
    Se actualiza el código para hacer la sincronización del clock utilizando la biblioteca de RadioHead ubicada en internet
    [project.cfg]
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2022-04-01 Se borra carpeta RadioHead
    Carpeta que se descomprimió para observar la función modificada
    [project.cfg]
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2022-05-22 Comunicación entre robots
    Se agrega la comunicación con direccionamiento a los robots y la comunicación entre ellos se realiza de manera correcta.
    [PROE_COMBASE.ino, PROE_LOCOM.ino]
2022-06-13 Correciones generales y mejoras a algoritmo de exploracion y encoders
    Feather M0
    Cambios:
    1. Corrección a formula de control PID
    1.1. Error: la parte integral se calculaba como producto de sumatoria, debe ser sumatoria de productos
    1.2. Valores de constantes PID modificadas para funcionar con corrección
    2. Tiempo de muestreo aumentado a 100 ms (100000 us)
    2.1. El tiempo de muestreo anterior no permitía obtener suficiente información sobre la velocidad de las ruedas por lo que el PID reaccionaba violentamente a cambios que veía como muy grandes entre cada muestra.
    2.2. Nuevo tiempo de muestreo permite ver ≈40 pulsos del encoder dando más precisión a cálculo de velocidad, anteriormen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
    [Calibracion_Completa.ino, PROE_COMBASE.ino, PROE_DETOB.ino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]
2022-06-23 Calibración en código general, correciones
    1. Sincronización movida a setup para evitar perder ciclos en ejecución
    2. Separado error máximo integral para velocidad y giro, al pedir valores grandes a la función Giro() el valor integral se disparaba provocando oscilación
    3. Agregado ciclo de trabajo para giro de calibración, reduce la velocidad para obtener los puntos necesarios de calibración
    4. Disminuido tamaño de lista de obstáculos anteriores, consumía la mayoría de la memoria ram (reducido uso de 91% a 22%)
    5. Función calibrar() reduce velocidad de giro y llama a funciones de calibración de MPU y magnetómetro
    6. AsignarDireccionRWM, eliminado código r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
    [Calibracion_Completa.ino, PROE_DETOB.ino, PROE_LOCOM.ino]
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2022-08-09 Correciones a selección de dirección y calibración de magnetometro
    1. Función Giro(): valores positivos de ángulo resultan en giros con el reloj.
    2. Corrección a RevisaObstaculoPeriferiaMemoria:
    a. Ignora “obstáculos” que no necesitan cambio de dirección (batería, temperatura).
    b. Error en posición de obstáculos respecto a la posición actual.
    3. Función RandomWalkconMemoria:
    a. Simplificada selección de dirección.
    b. Cambiada selección de dirección por la corrección a la función Giro().
    4. Funcion AvanzarCoordenada:
    a. Comentados serialprint.
    5. Calibración de magnetómetro:
    a. Aumentada la cantidad de muestras a tomar en tiempo de calibración (de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
    [PROE_DETOB.ino, PROE_LOCOM.ino]
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2022-08-12 Experimento objetivo 2
    Se realiza el experimento para validar el porcentaje de entrega de los mensajes en los robots y el porcentaje de error que tienen los datos un vez que llega el mensaje
    [PROE_LOCOM.ino]
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2022-09-11 Update PROE_LOCOM.ino
    Cambios LOCOM:
    1. Optimizaciones a código de calibración de magnetómetro
    a. Cambiadas listas de datos de float a short
    b. Mejorado calculo de segundos momentos de inercia para evitar condición de overflow
    c. Agregada salida de datos de calibración en el puerto serial de ser necesario verificarlos
    2. RevisaObstaculoPeriferiaMemoria: corrección a calculo de ángulo de obstáculos
    [PROE_LOCOM.ino]
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2023-02-01 Final Sistema de Visión 2.0
    Cambios adicionales
    [ExportadorCodigosTamañoReal.dwg]
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2024-02-19 Revert "Mejoras en comunicación de obstáculos"
    This reverts commit b0cc34ff267e1b05a7bd67d08c4c769960fb5324.
    [PROE_DETOB.ino, PROE_LOCOM.ino]
2024-02-19 Revert "Update PROE_DETOB.ino"
    This reverts commit b58f5020a11473fa970986eac7e57eb56efb027f.
    [PROE_DETOB.ino]
2024-02-19 Revert "Cambio valor inicial distancia"
    This reverts commit e55d72b92ebd481dc4a8e158bf1ef513130a2f0d.
    [PROE_DETOB.ino]
2024-04-02 Update PROE_DETOB.ino
    Se solucionan problemas de exceso de mensajes enviados al feather
    [PROE_DETOB.ino]
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2024-07-29 new test data
    [Period and frequency data.csv, Sampling data.csv]
2024-10-04 Update on experimental data
    [Figure8bottom_timedata.csv, Figure8botttom_rawdata.csv, Figure8top_rawdata.csv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]
2025-02-21 Agregué los últimos archivos de optimización de rutas funcionales tanto en linea como offline. También incluyendo programa de R para procesamiento de datos y un documento que explica los contenidos d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
    [MatrizPeligro.csv, Principal.csv, Resumen.csv]
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
